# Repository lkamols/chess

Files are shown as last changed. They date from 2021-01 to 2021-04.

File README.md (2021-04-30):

# chess

Building a physical chess set that plays against a human player. Human moves will be detected with magnets and the 'CPU' will move pieces against the player.

## Description

The project is being done using a raspberry pi 3 and various other components. The board being constructed is 8x12, with 8x8 for the chess board, and an extra 8x2 on each side for dead pieces. Every square has an RGB neopixel LED underneath it, so the board can be updated to any configuration. The board itself is not coloured as that will be communicated using the LEDs.

## Code

Currently I have implemented a chess engine that can run a game (located in Code), with a framework for the important functions for the game display and movement which will come further down the line. This contains some functions currently being used to debug the constructed circuit.

## Chess Board Construction

The chess board is being 3D printed, made up of 24 components, laid out as below. 



Each of these pieces was designed using Autodesk Inventor (files in Board/Pieces)[detection_schematic.pdf](https://github.com/lkamols/chess/files/6402259/detection_schematic.pdf)
 and was then 3D printed, they look like this. 



These then interlock to form the whole board, there are holes throughout which have metal rods to provide structural support.



## Piece Detection

A circuit schematic for the piece detection circuit is shown below. This makes use of decoders and multiplexers to reduce the number of pins on the Raspberry Pi that are required to 8. To detect any particular square, one of the input (horizontal) lines is driven high (all others low) and then reading any of the output (vertical) lines gives whether or not there is a piece (magnet) at any particular square. At each square there is a reed switch (one I designed myself, discussed later) which will act as a switch that is connected when there is a magnet nearby.



## Reed Switches
I originally bought some reed switches for piece detection, but these don't work for what I need. The reason for this is the magnetic field orientation required. To move the pieces later with an electromagnet, they need to have the north/south poles vertically. But the only way to reliably execute this with a reed switch is to orient them vertically, which would make the board thick and I didn't want to do that, so I designed my own reed switches, shown below. These reed switches are contained in the same compartment as the neopixel LED to save space.



The small long component is a strip of iron I got from pulling apart an old transformer with a piece of copper tape on one side. This is placed in the other compartment next to the LED (but cannot ever touch the LED because of its shape). This is then glued to the bottom of the other, flatter piece as shown below.



This is then placed into the chess board facing the opposite way. When a magnet is placed on the top surface, the metal strip is attracted to it, and completes the circuit, allowing current to flow through. If there is no magnet nearby the piece of iron strip falls back down with gravity and disconnects the circuit. In practice this has been very reliable, and does not depend at all on the orientation of the magnet, which fixes the problem with an existing reed switch.

## LED circuitry
Each square has a Neopixel RGB LED in it so that the board can change colours at any time. The Neopixel LEDs are connected to GPIO18 on the Raspberry pi. The neopixel library is used to send signals for controlling the colours displayed, it uses PWM and DMA to ensure the signals are correct even with the Pi's operating system running. There is a level shifter to convert from the 3.3V of the Raspberry Pi to the 5V required for the neopixels. Capacitors are included close to the neopixel to help avoid any damage caused by spikes. The wiring is shown below, with 96 LEDs being repeated, one for each square.



## Putting it all together
The reed switch and LED are placed in the same compartment for each square, shown above. These then have wires soldered to the copper tape which is then fed through the holes in the chess board, and wired to copper tape on the underside of the chess board. A picture of the underside of the board is shown below.



This soldering process is about one third complete, life has taken over which has pushed this further down the priority list unfortunately.

## Moving Pieces
I intend on building a 3D printer style movement system under the board which moves an electromagnet. To move a piece, the electromagnet would be moved underneath the piece, turned on, moved to the destination, and the electromagnet turned off. Currently I have been doing some experiments with electromagnets to determine the strength of electromagnet I would need to effectively move one piece (but not more). I have been doing this by constructing an electromagnet myself, pulling apart an old transistor to salvage iron pieces for the iron core and the wiring. I have made two electromagnets so far, shown below.



## Chess Pieces
Using Autodesk Inventor I have designed my own chess pieces, I went for a quite minimalistic theme, they are shown below and can be found in Board/Chess-Pieces.



They each have a small compartment at the bottom to insert a magnet, the magnets being used are rectangular floristry magnets.

## How Will the Knight Move?
Everyone's favourite question, the board is quite large, for this particular problem, with the pieces being on the smaller side. The horse will then be able to travel between two pieces, moving through the corners of the squares

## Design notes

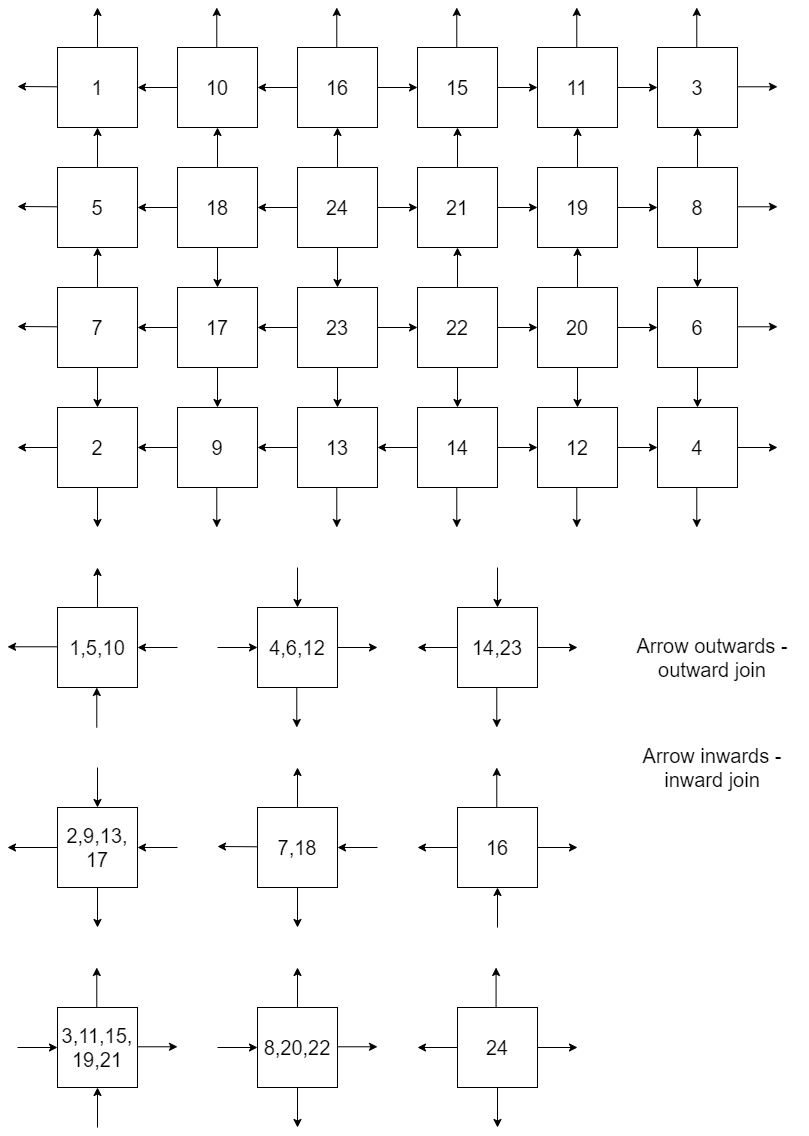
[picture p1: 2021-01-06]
Board/Pieces/piece-layout.png

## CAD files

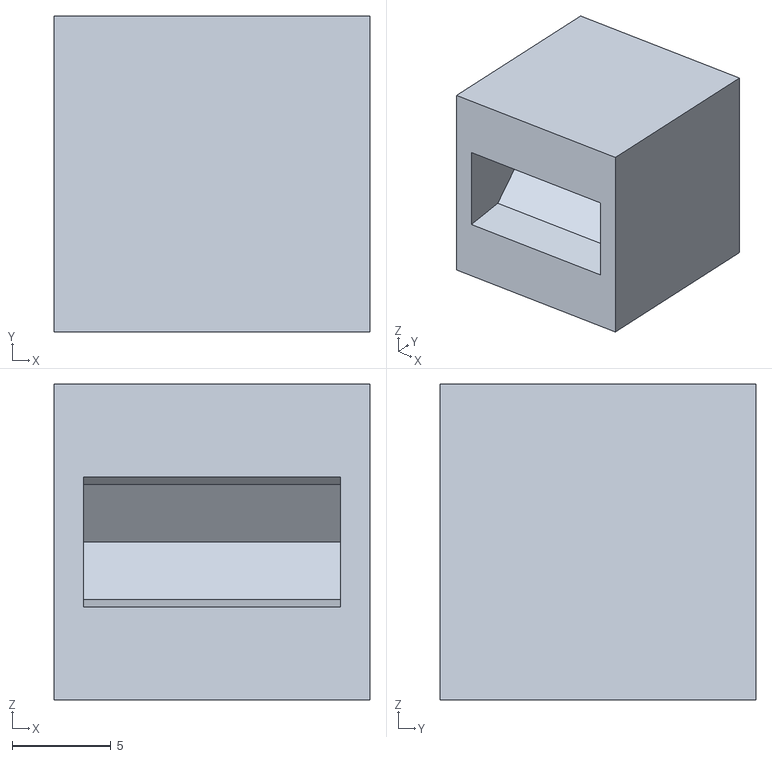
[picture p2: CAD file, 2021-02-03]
Board/Chess-Pieces/pawn.stl
16.0 x 16.0 x 16.0

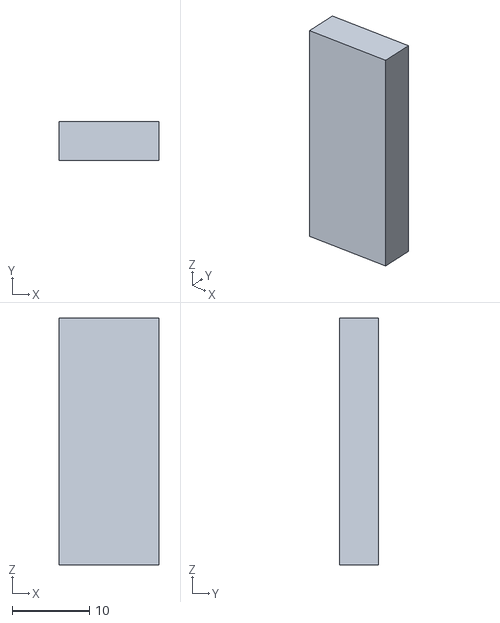
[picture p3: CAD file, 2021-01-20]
Board/Experimentation/long-reed.stl
13.0 x 5.00 x 32.0

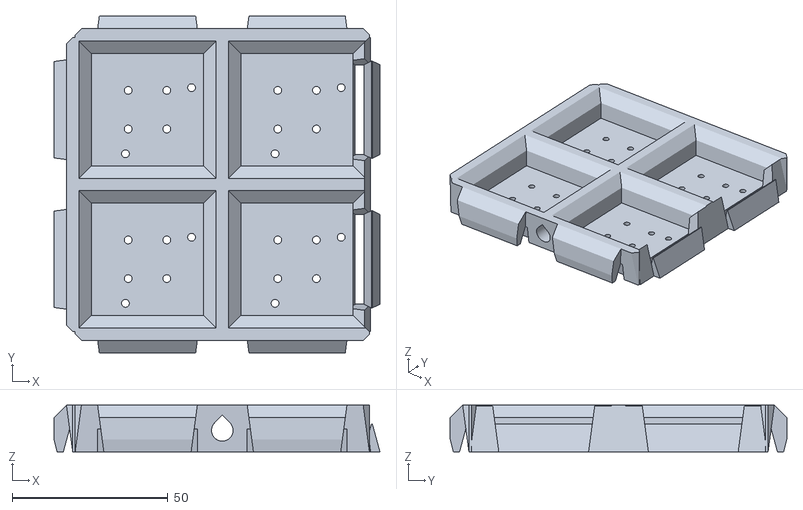
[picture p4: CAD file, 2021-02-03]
Board/Printing/8.stl
104.6 x 108.0 x 15.0

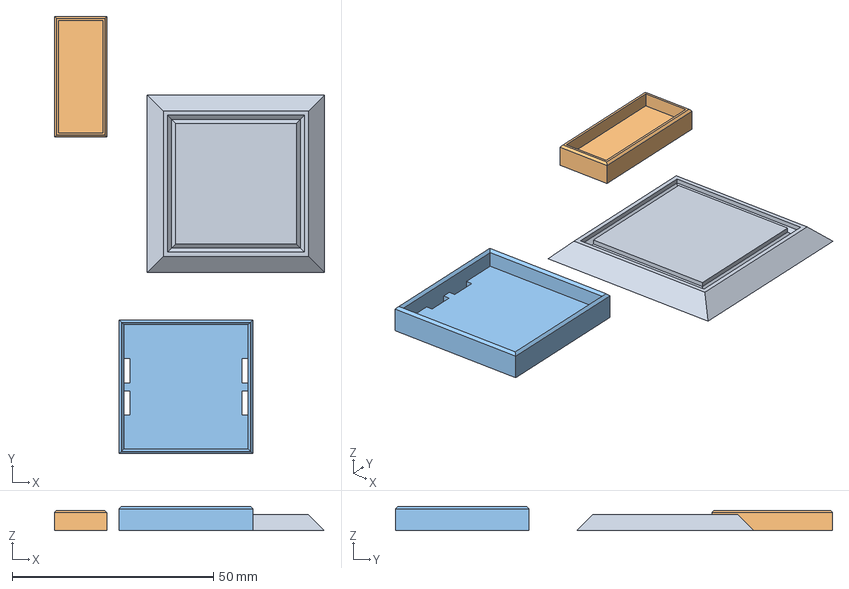
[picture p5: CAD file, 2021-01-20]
Board/Printing/Templates/clear-abs.3mf
67.0 x 108.5 x 6.00 mm
clear-square-notched.stl
reed-switch-compartment.stl
led-compartment.stl

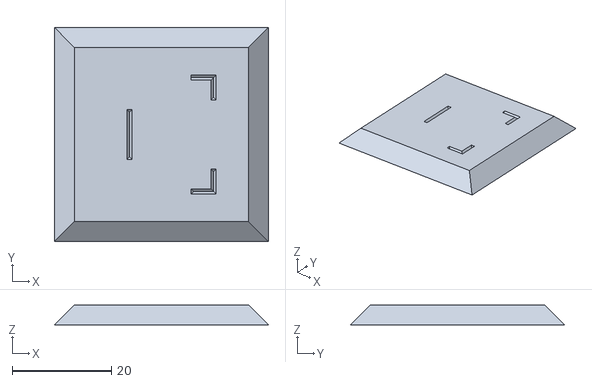
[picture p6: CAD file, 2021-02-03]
Board/Reed-Switch/clear-square-outlined.stl
43.2 x 43.2 x 4.00

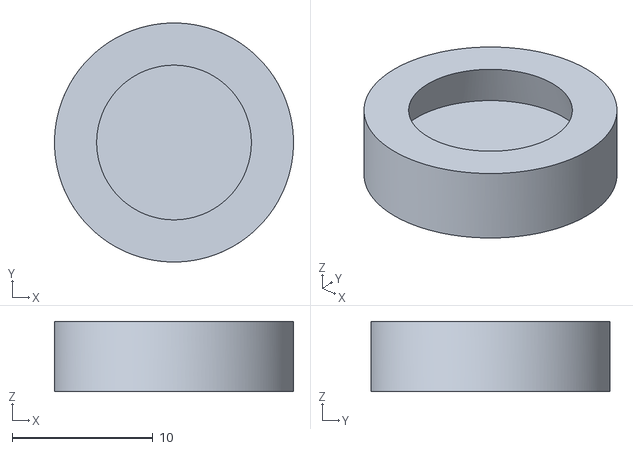
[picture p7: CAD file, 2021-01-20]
Board/Experimentation/circle-reed.stl
17.0 x 17.0 x 5.00

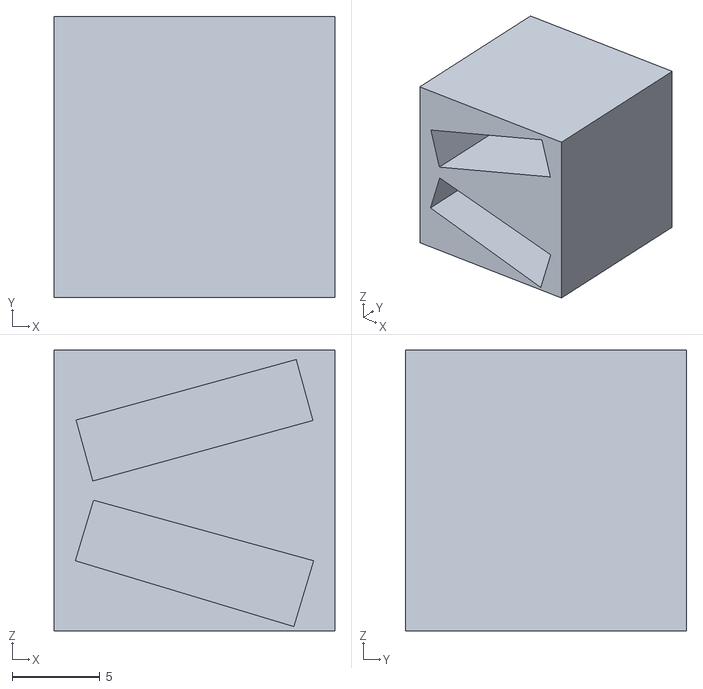
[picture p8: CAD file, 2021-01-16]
Board/Printing/pawn-2.stl
16.0 x 16.0 x 16.0

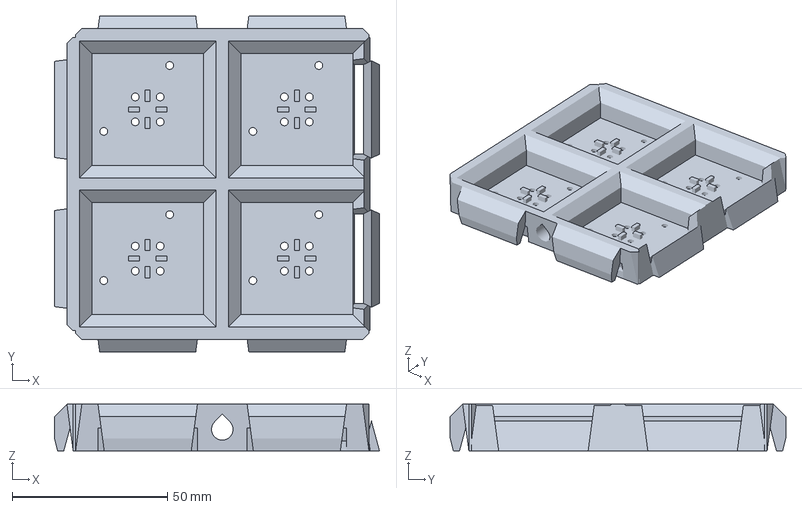
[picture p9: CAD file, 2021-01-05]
Board/Printing/Templates/black_pla.3mf
104.6 x 108.0 x 15.0 mm

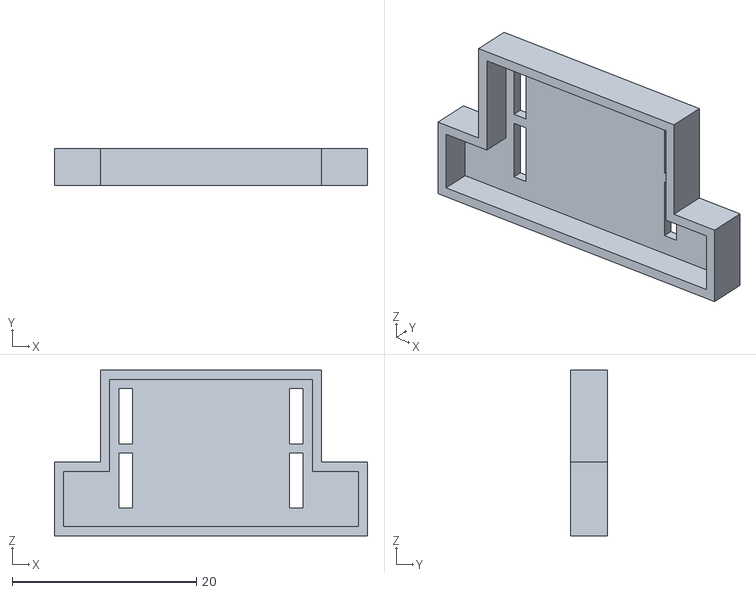
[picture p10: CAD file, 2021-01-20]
Board/Reed-Switch/led-reed-compartment.stl
34.0 x 4.00 x 18.0

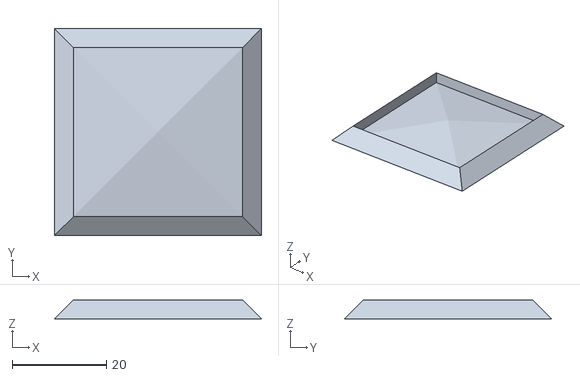
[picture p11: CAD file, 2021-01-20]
Board/Experimentation/clear-square-inset.stl
44.0 x 44.0 x 4.00

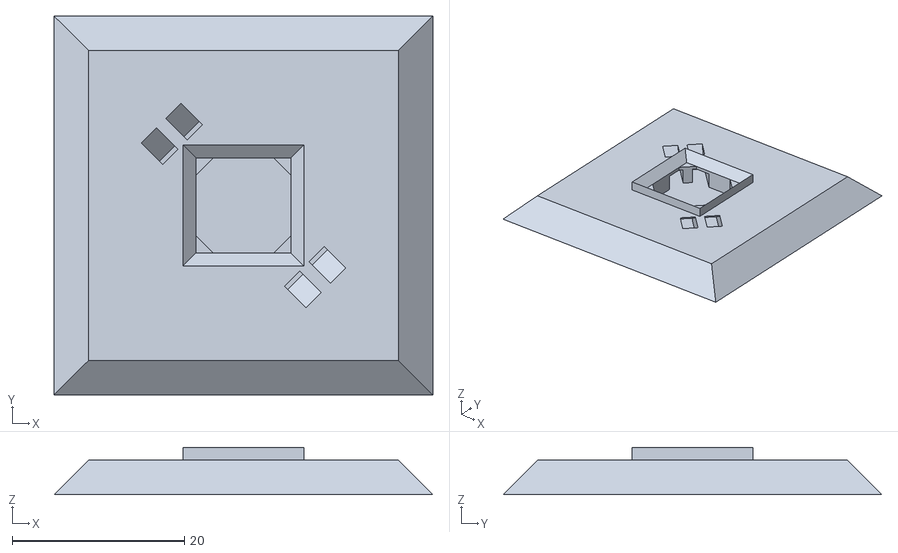
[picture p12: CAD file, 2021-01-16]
Board/Printing/clear-square-reed.stl
44.0 x 44.0 x 5.50

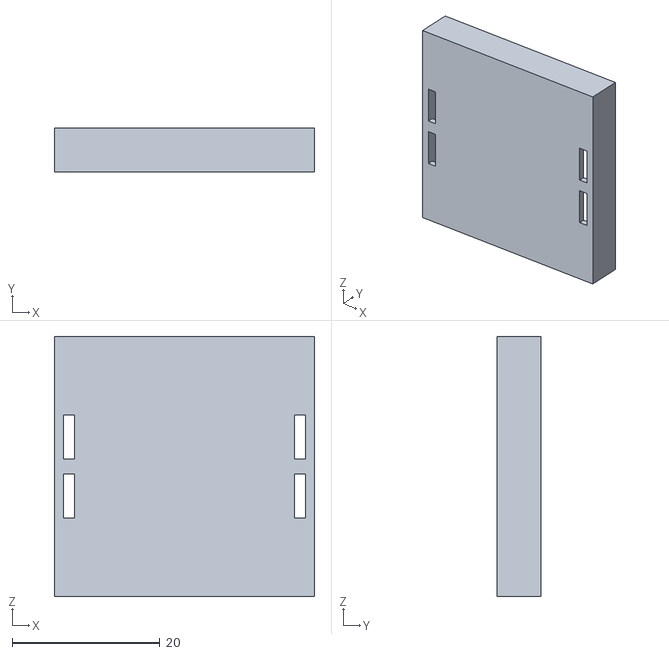
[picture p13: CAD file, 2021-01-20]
Board/Experimentation/led-compartment-2.stl
35.2 x 6.00 x 35.2

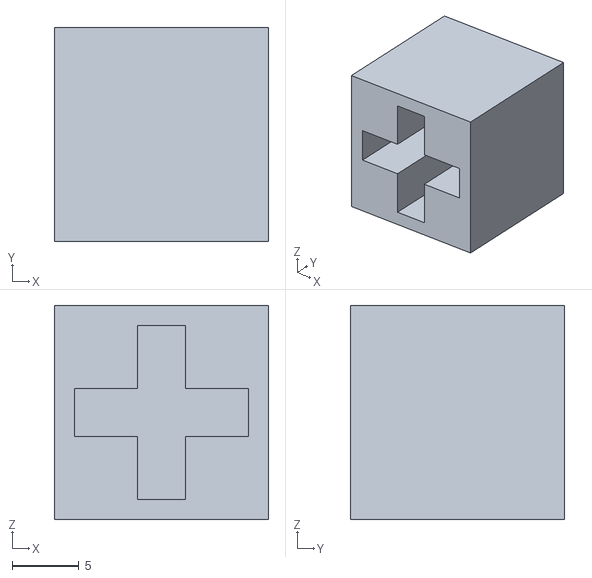
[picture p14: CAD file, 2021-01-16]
Board/Printing/pawn.stl
16.0 x 16.0 x 16.0

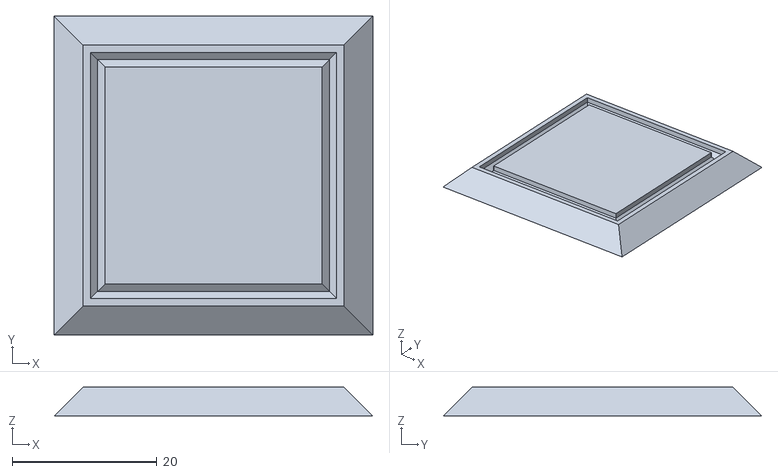
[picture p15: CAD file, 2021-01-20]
Board/Experimentation/clear-square-notched.stl
44.0 x 44.0 x 4.00

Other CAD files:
Board/Printing/clear-square-reed-2.stl
Board/Experimentation/led-compartment.stl
Board/Printing/electromagnet-ending.stl
Board/Experimentation/reed-switch-compartment.stl
Board/Chess-Pieces/OldVersions/pawn-2.0001.ipt
Board/Chess-Pieces/OldVersions/pawn.0006.ipt
Board/Chess-Pieces/OldVersions/queen.0001.ipt
Board/Chess-Pieces/OldVersions/tiered-king.0001.ipt
Board/Chess-Pieces/bishop.ipt
Board/Chess-Pieces/horse.ipt
Board/Chess-Pieces/king.ipt
Board/Chess-Pieces/pawn.ipt
Board/Chess-Pieces/queen.ipt
Board/Chess-Pieces/rook.ipt
Board/Chess-Pieces/tiered-king.ipt
Board/Components/OldVersions/clear-square-reed-2.0001.ipt
Board/Components/OldVersions/clear-square-reed.0003.ipt
Board/Components/OldVersions/electromagnet-ending.0001.ipt
Board/Components/base.iam
Board/Components/clear-square-hollow.ipt
Board/Components/clear-square-reed-2.ipt
Board/Components/clear-square-reed.ipt
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

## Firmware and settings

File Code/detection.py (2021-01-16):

from gpiozero import LED, Button
import time

#decoder inputs
DEC_C = 17
DEC_B = 27
DEC_A = 22
#mux inputs
MUX_C = 23
MUX_B = 24
MUX_A = 25
#mux outputs
M1_OUT = 12 #output of multiplexer controlling columns 0-5
M2_OUT = 4 #output of multiplexer controlling columns 6-11


"""
generally set an output to a value, 0 for off, otherwise on
pin - a gpiozero LED variable
"""
def set_output(pin, value):
    if value == 0:
        pin.off()
    else:
        pin.on()

"""
read an input from a GPIO declared button, just a rename to 
make it more clear
pin - a gpiozero Button variable
"""
def read_input(pin):
    return 1 - int(pin.is_pressed) #this is opposite to intuitive

"""
set the values for a 3 bit control of a logic chip.
pin0, pin1, pin2 - the LEDs/pins to control
val - the value to write to these pins, 0 <= val <= 7
"""
def three_val_input(pin0, pin1, pin2, val):
    set_output(pin0, val & (1<<0))
    set_output(pin1, val & (1<<1))
    set_output(pin2, val & (1<<2))


class Detection:
    """
    init function, initialises the mux to zero
    """
    def __init__(self):
        self._init_mux()
        self._init_decoder()
        self._board = []
        for i in range(8):
            self._board += [[0]*12]
      
    """
    initialise the mux to be all set as outputs
    """
    def _init_mux(self):
        #declare shared MUX inputs as LEDs for on/off functionality
        self._muxC = LED(MUX_C)
        self._muxB = LED(MUX_B)
        self._muxA = LED(MUX_A)
        #declare the MUX outputs as buttons so that they can be read from
        self._m1_out = Button(M1_OUT)
        self._m2_out = Button(M2_OUT)
    
    """
    initialise the decoder inputs to be set as outputs
    """
    def _init_decoder(self):
        #declare decoder inputs as LEDs for on/off functionality
        self._decC = LED(DEC_C)
        self._decB = LED(DEC_B)
        self._decA = LED(DEC_A)

    """
    Set the mux inputs to a specific value, 0 <= val <= 7
    """
    def set_mux(self, val):
        three_val_input(self._muxA, self._muxB, self._muxC, val)

    """
    Set the decoder inputs to a specific valu, 0 <= val <= 7
    """
    def set_decoder(self, val):
        three_val_input(self._decA, self._decB, self._decC, val)

    """
    Read a specific square, for debugging purposes
    """
    def read_square(self, row, col):
        #the row is controlled by the decoder
        self.set_decoder(row)
        #the column is controlled by the muxes
        self.set_mux(col % 6)
        #then choose output based on the column
        #0-5 are on the first mux
        #6-11 are on the second mux
        if col < 6:
            return read_input(self._m1_out)
        else:
            return read_input(self._m2_out)

    """
    print the current detected board status
    """
    def print_board(self):
        for row in range(8):
            print(self._board[row])


    """
    Update the detected board storage
    """
    def update_board(self):
        global _board
        for row in range(8):
            self.set_decoder(row)
            for mux_val in range(6):
                self.set_mux(mux_val)
                self._board[row][mux_val] = read_input(self._m1_out)
                self._board[row][mux_val + 6] = read_input(self._m2_out)

if __name__ == "__main__":
    det = Detection()
    det.print_board()
    while(1):
        time.sleep(5)
        det.update_board()
        det.print_board()
  

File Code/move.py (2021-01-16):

from constants import *
"""
Class defining a move, takes a piece to an end location
"""

def pos_to_square(row, col):
    return chr(ord('a') + col) + str(row+1)

class Move:

    """
    constructor.
    piece -  the piece being moved
    start_row/start_col - the starting position of the piece
    end_row/end_col - the ending position of the piece
    kill - reference to the piece being killed, None if no kill occurs
    en_passant - True if this move is an En Passant, false otherwise
    castle - the ID of the castle if the move is a castle, NO_CASTLE otherwsie
    promotion - the choice of promotion from "q", "n", "r", "b" if the move is a promotion, None otherwise
    """
    def __init__(self, piece, start_row, start_col, end_row, end_col, 
            kill=None, en_passant=False, castle=NO_CASTLE, promotion=None):
        self.piece = piece
        self.start_row = start_row
        self.start_col = start_col
        self.end_row = end_row
        self.end_col = end_col
        self.kill = kill
        self.en_passant = en_passant
        self.castle = castle
        self.promotion = promotion

    """
    the move as a string
    """
    def short_representation(self):
        string = pos_to_square(self.start_row, self.start_col) + \
                pos_to_square(self.end_row, self.end_col)
        #then if there is a promotion, dictate which promotion it is
        if self.promotion != None:
            string += self.promotion
        return string

    """
    create a duplicate move instance
    """
    def duplicate(self):
        return Move(self.piece, self.start_row, self.start_col, self.end_row, self.end_col,
                self.kill, self.en_passant, self.castle, self.promotion)

    """
    full move information as a string
    """
    def to_string(self):
        ret = "%s at %s " % (self.piece.get_name(), pos_to_square(self.start_row, self.start_col))
        if self.kill == None:
            ret += "moves to "
        else:
            ret += "kills %s at " % self.kill.get_name()
        ret += pos_to_square(self.end_row, self.end_col)
        if self.promotion != None:
            ret += " promoting to %s " % self.promotion
        elif self.castle != NO_CASTLE:
            ret += " by castling "
        ret += " (%s)" % self.short_representation()
        return ret

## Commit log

2021-01-05 added inventor files
    [19.iam, 19.stl, 20.iam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]
2021-01-06 made all the board pieces
    [1.0001.iam, 1.iam, 1.stl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]
2021-01-08 basic chess functionality working, still missing some things like castling and promotion
    [board.py, game.py, move.py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]
2021-01-09 added fen representation to board output
2021-01-16 Some more 3d printing work
    [circle-reed.ipt, circle-reed.stl, clear-square-reed-2.0001.ipt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]
2021-01-20 some reed switch design work
    [circle-reed.0001.ipt, circle-reed.ipt, circle-reed.stl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]
2021-02-03 some more progress
    [20.iam, 8.iam, 8.stl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]
